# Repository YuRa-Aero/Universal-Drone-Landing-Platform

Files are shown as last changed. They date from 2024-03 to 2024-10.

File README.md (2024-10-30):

# Универсальная посадочная платформа для дронов

[][cc-by-nc]

[cc-by-nc]: https://creativecommons.org/licenses/by-nc/4.0/
[cc-by-nc-shield]: https://img.shields.io/badge/License-CC%20BY--NC%204.0-lightgrey.svg

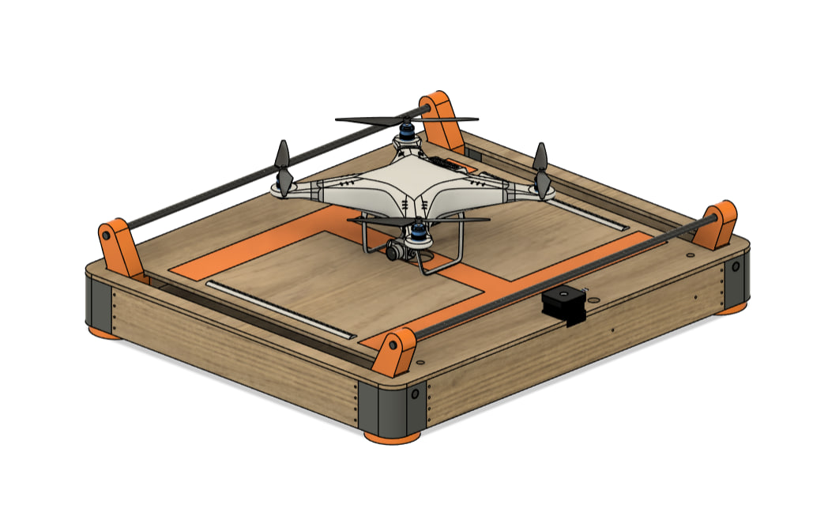
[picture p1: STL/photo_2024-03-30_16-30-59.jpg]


В данном проекте реализуется полная разработка готового изделия по техническому заданию с нуля в сжатый срок - 5 дней.

ТЗ *(подробнее см "ТЗ.pdf)* : разработать посадочную платформу для дронов различных размеров с фиксацией квадрокоптера после посадки

В ходе выполнения работы:
* Сделано эскизное проектирование
* Создан чертеж платформы *(Для изучения моделей см. "Чертеж.pdf)*
* Смоделирована подробная 3д модель, каждый узел подготовлен к 3д печати *(Для изучения моделей см. папку "STL")*
* Выполнена робототехническая часть
* Разработана инструкция по сборке
* Расчитана себестоимость с учётом производства
* Оформлена документация в формате PDF
## *Для более детального ознакомления с проектом см. "Документация.pdf" - 33стр.*
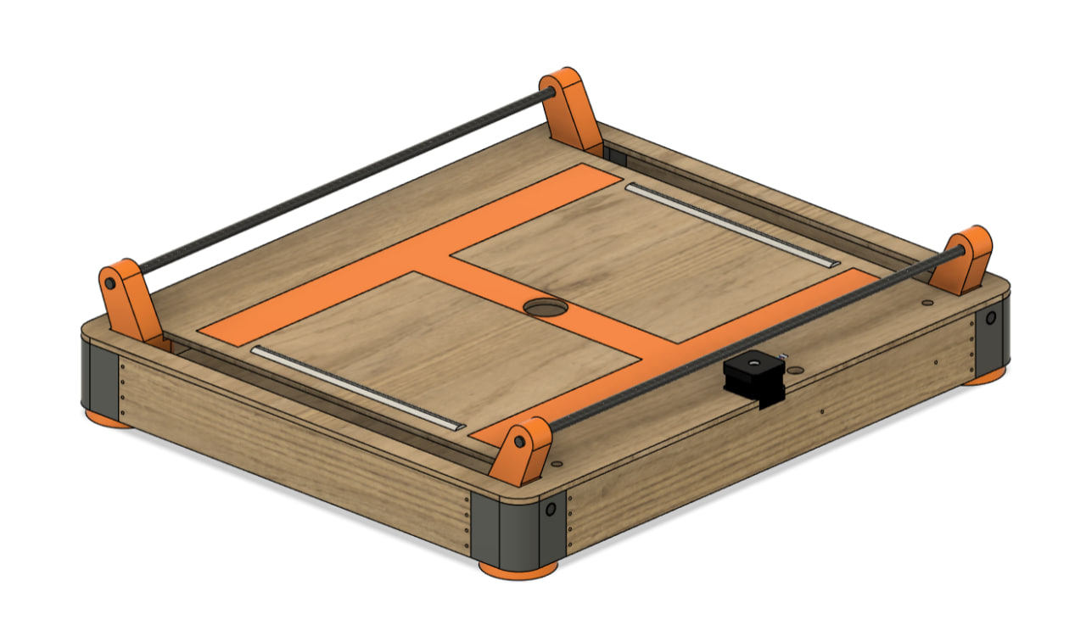
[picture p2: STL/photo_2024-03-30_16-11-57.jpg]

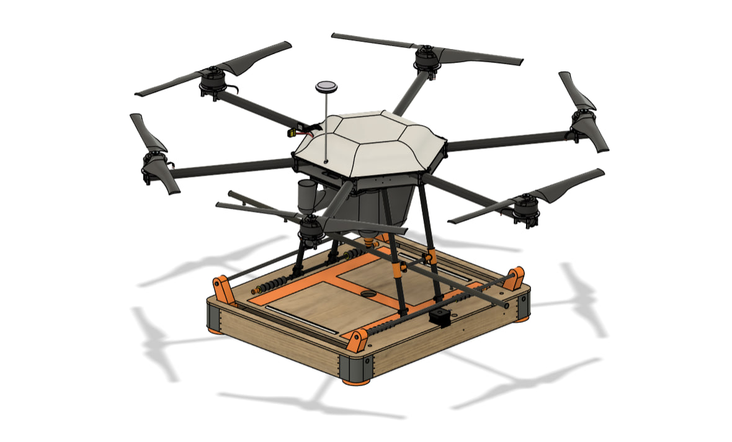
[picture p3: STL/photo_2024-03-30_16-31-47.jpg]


[][cc-by-nc]

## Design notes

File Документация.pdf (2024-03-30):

ЛНИП г. Королев

Проектная работа

### УНИВЕРСАЛЬНАЯ ПОСАДОЧНАЯ ПЛАТФОРМА ДЛЯ КВАДРОКОПТЕРОВ

Работа выполнена в рамках конкурсного задания на отбор в Артек 2024 «Реализация поставленного кейса на тему БЛА»

Выполнил:
Ученик 10 Б класса Куликов Юрий Наставник:
Куликов А.П.
2024

### Оглавление

Определение и разработка механической системы фиксации квадрокоптера на платформе после посадки. Определение необходимых дополнительных модулей и сенсоров с описанием их

### 8. По итогам анализа разработанного прототипа Платформы были выявлены следующие

0. Введение
0.1 Проблема
Посадка БЛА один из самых важных этапов полёта. На этом этапе происходит большинство случаев поломок БЛА, в том числе по следующим причинам:
- неровной поверхности на зоне посадке (склоны, рытвины, высокая трава и другие антропогенные факторы).
- неверное позиционирование зоны посадки оператором, в том числе через на FPV дронах
- неверное позиционирование посадочной зоны из-за плохих погодных условий – дождь, туман, тёмное время суток.
Также одной из востребованных задач после приземления дрона, является задача уменьшения времени «сворачивания» и смены позиции запуска дрона. Эта задача стоит перед обслуживающей дрон командой (расчётом).
0.2 Актуальность
В современных условиях активного использования дронов для решения различных задач, возникает потребность создания приспособления-устройства решить описанную проблему. Автономные взлетно-посадочные платформы для беспилотных летательных аппаратов используются для решения задач различного рода, в том числе для автоматической доставки продуктов, для военных задач, задач мониторинга и орошения в агропромышленном комплексе.
0.3 Цель
Необходимо разработать универсальную посадочную платформу для квадрокоптеров (далее- Платформа), предназначенную для различных применений.
0.4 Задачи
Задание 1. Эскизное проектирование:
Нарисовать эскиз будущей платформы (может быть нарисован с помощью чертёжных принадлежностей на листе бумаги, или графического планшета, или CAD-системы).

Задание 2. 3D-моделирование:
Создать 3D-модель(и) посадочной платформы с учетом габаритов и весовых характеристик квадрокоптеров различных типов и моделей.
Задание 3. Робототехническая часть:
3.1. Разработать механическую систему фиксации квадрокоптера на платформе после посадки.
3.2. Предусмотреть места для крепления и подключения дополнительных модулей и сенсоров, описать их назначение.
Задание 4. Программирование:
Разработать код для управления подсветкой посадочной платформы в зависимости от расстояния до приземляющегося квадрокоптера.
Задание 5. Производство:
Определить необходимые материалы для изготовления посадочной платформы с учетом прочности и легкости.
Задание 6. Бюджет:
Определить бюджет проекта.

0.5 Основная концепция
Основные допущения при создании универсальной посадочной платформы для квадрокоптеров:
✓ В части универсальности выбирается определённое семейство дронов размерами от DJI Phantom до агрокоптеров с вместимостью бака до 16л. Для квадрокоптеров большего типоразмера нужна доработка данного решения, с условиями масштабируемости. Для квадрокоптеров меньшего размера актуальность наличия Платформы является низкой. Но и для них может быть разработана уменьшенная версия Платформы.
✓ При выборе материалов для изготовления отдаётся предпочтение в сторону деталей изготовляемых способом 3D печати. Количество деталей из других материалов минимизируется.
✓ Материалы из стали не используются из-за сложности их обработки.
✓ В части электронной базы и датчиков решается задача баланса между стоимостью и функциональностью. Компонент выбирается за минимальную стоимость с необходимой функциональностью.
✓ Также решается задача максимально быстрого создания рабочего прототипа изделия, без выхода на промышленное производство, для отработки работоспособности прототипа
✓ Автономность. Предполагается автономное питание и обслуживание-переноска одним человеком.
✓ Предполагается использование в закрытых помещениях и на открытом воздухе. ✓ Предполагается что Платформа будет эксплуатироваться в температурных режимах от -5 до +40 градусов. При более низких температурах нужно вводить элементы подогрева, смазку и менее хрупкие материалы. При более высоких температурах возможен перегрев электронного блока и нарушение геометрии деталей распечатанных методом 3d печати.

0.6 Требования к оформлению результатов проекта в виде файлов и документов:
1. Документация в формате PDF:
✓ В этом файле должны быть описаны этапы выполнения задания.
✓ Разработанные эскизы, скриншоты хода выполнения работы, а также фотографии, должны быть приложены в этот файл.
✓ В этом файле должен быть представлен весь программный код, который был использован для выполнения задания.
2. 3D-модели в формате STL:
✓ Каждая модель должна быть представлена в отдельном файле с соответствующим названием.
✓ Файлы должны быть сохранены в формате STL, который является стандартом для обмена 3D-моделями.
1. Задание 1: Эскизное проектирование.
Создание эскиза-чертежа будущей платформы с помощью CAD-системы.

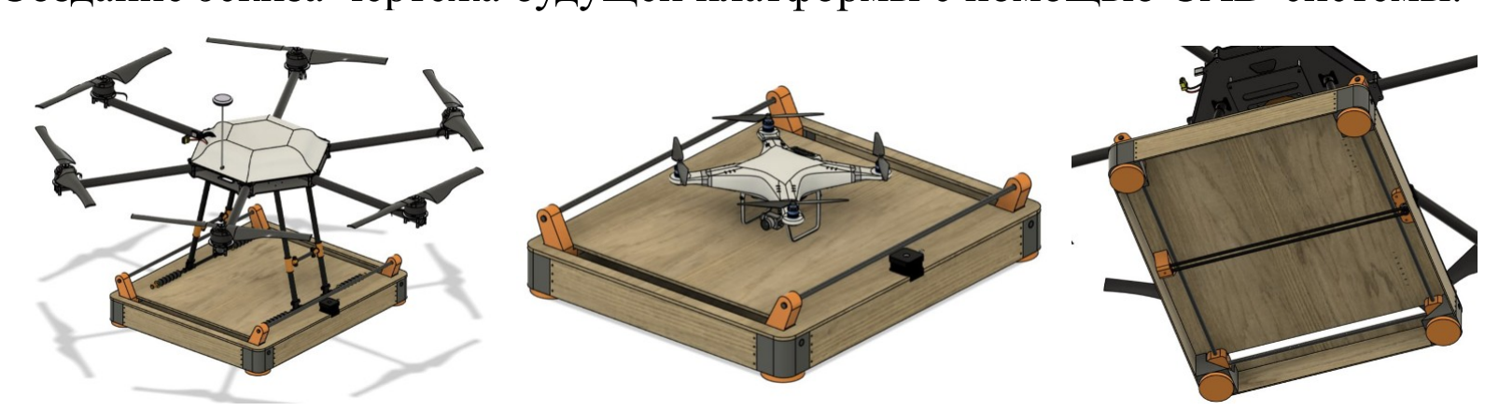
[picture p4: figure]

Рис. 1.1. Эскиз Платформы выполенный в Fusion360.

Описание принципов работы Платформы: Платформа устанавливается на поверхность, ножки позволяют производить небольшую регулировку для выравнивания. Включается питание платформы и переходит в режим ожидания прибытия БЛА. В это время для лёгкости обнаружения БЛА Платформа подсвечивается. Платформа оборудована дальномером и в момент обнаружения БЛА, готового для приземления, включается цветная подсветка. После приземления БЛА на платформу включаются механические захваты-толкатели, которые позиционируют и фиксируют БЛА. После нажатия кнопки оператором, захват освобождает БЛА для взлёта или снятия с Платформы. После этого Платформа заново переходит в режим готовности принятия нового БЛА.

Приведенные выше пластиковые детали (имеющие серый и оранжевый цвет на рендерах) были подготовлены к изготовлению на 3D принтере. Для этого модели деталей, разработанные в среде Fusion 360, были экспортированы в формат, использующийся в технологии быстрого прототипирования 3-D печати для хранения трехмерных моделей объектов stl. Полученный файл обрабатывается программой Prusa Slicer, которая и управляет режимом печати модели на принтере Prusa MK3S+.
Далее сборка Платформы в формате step была импортирована в программу Компас-3Д для создания чертежа модели по ГОСТу.

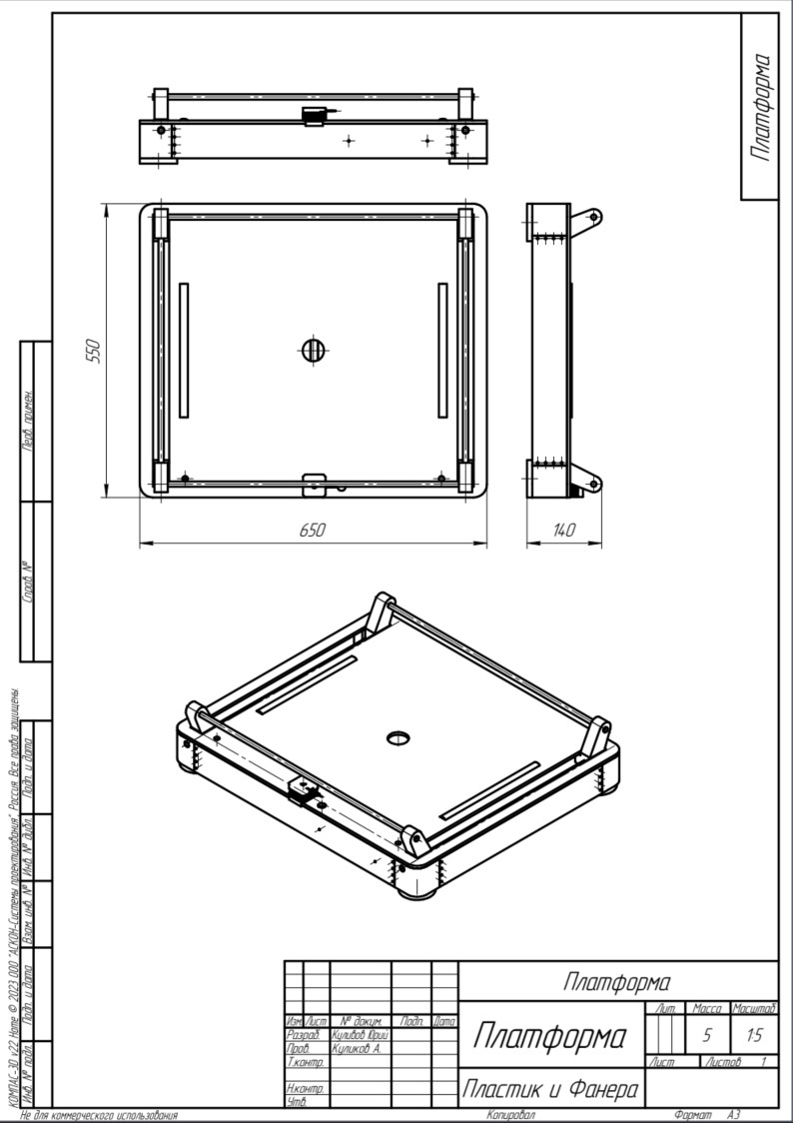
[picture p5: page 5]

Рис. 1.2 Чертёж в по ГОСТ выполенный в CAD системе КОМПАС-3D

Заключение: в ходе выполнения Задания 1 создан полноценный чертеж-эскиз Платформы:
- демонстрирующий идею проекта
- демонстрирующий принцип работы проекта,
- демонстрирующий его элементы
- эскиз образмерен и выполнен в цифровом виде в CAD-системе
- чертёж оформлен по ГОСТу
2. Задание 2: 3D-моделирование.
Создание 3D-модель(и) посадочной платформы с учетом габаритов и весовых характеристик квадрокоптеров различных типов и моделей
Проведён анализ текущих видов распространённых квадрокоптеров и видов их формы для разработки универсального захвата (Рис. 2.1 – Рис.2.4). Также дополниетльно, вне границы конкурсного задания рассмотрены мультикоптеры (Рис. 2.5)

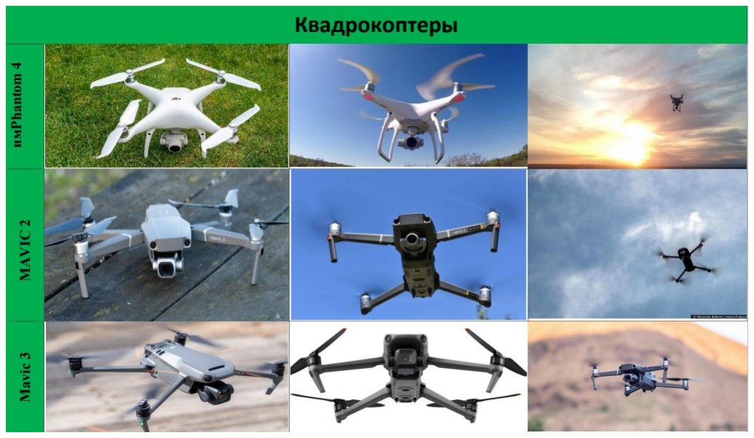
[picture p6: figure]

Рис. 2.1 Квадрокоптеры типа Mavic 2 Mavic 3 Phantom 4.

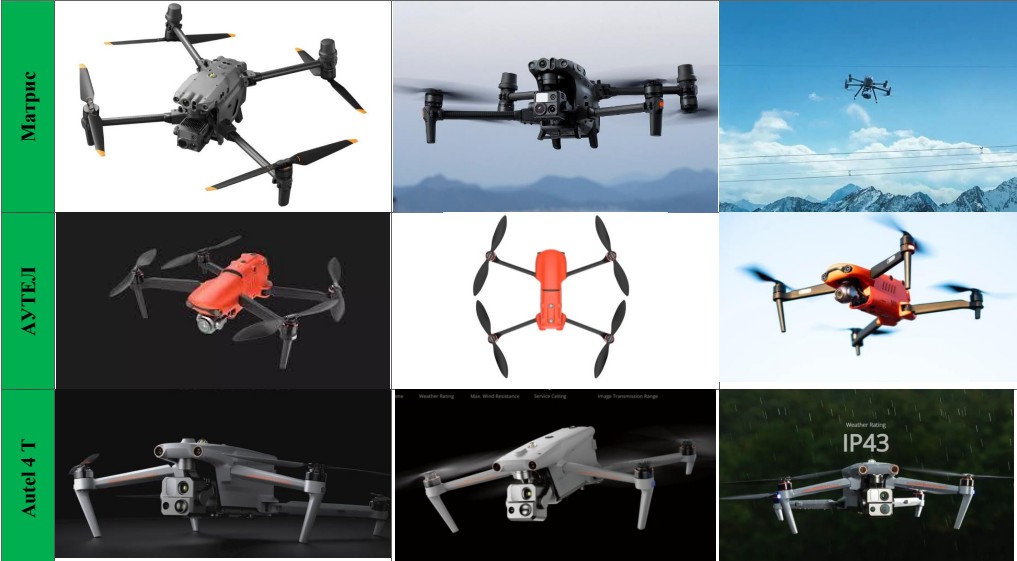
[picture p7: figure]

Рис. 2.2 Матрис, АУТЕЛ, Autel 4T.

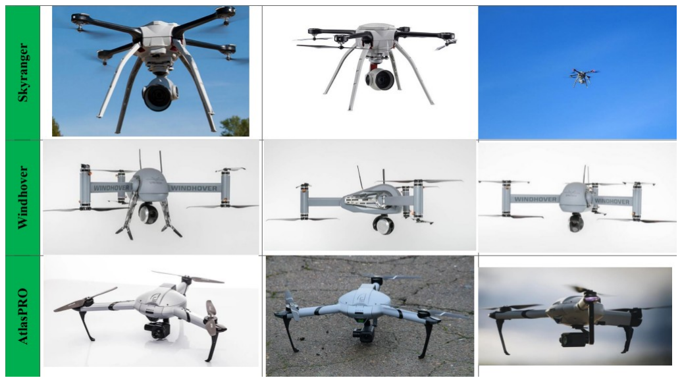
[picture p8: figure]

Рис. 2.3 Квадрокоптеры типа Skyranger, WindHover, AtlasPro.

Рис. 2.4 Квадрокоптеры типа Kargu m ½ Skydio X2.

Рис. 2.5 Мультикоптеры Matrice 600. Были проанализированы текущие решения посадочных платформ и типов захвата. Наиболее полно информация раскрыта статьёй на Хабре. [12]. Наиболее перспективным видом толкателей посчитал W и V образные толкатели. См. Рис. 2.6 Где слева: посадочная платформа с W-образными толкателями для позиционирования: 6 - БПЛА; 401 - толкатели W-образными кромками. Справа: Посадочная платформа с V-образными толкателями для позиционирования: 810 - ножка БПЛА; 220 - толкатели с V-образными кромками.

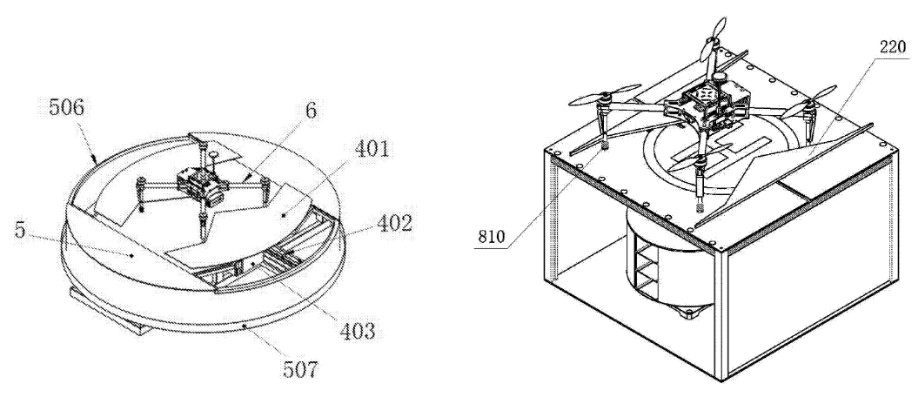
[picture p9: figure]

Рис. 2.6 W и V образные толкатели

Но учитывая, что большинство агродронов (см. Рис 2.7) используют опорную конструкцию в виде пользьев, такой вид толкателей не стал выбирать. Так как для полозьев данный вид захвата не эффективен

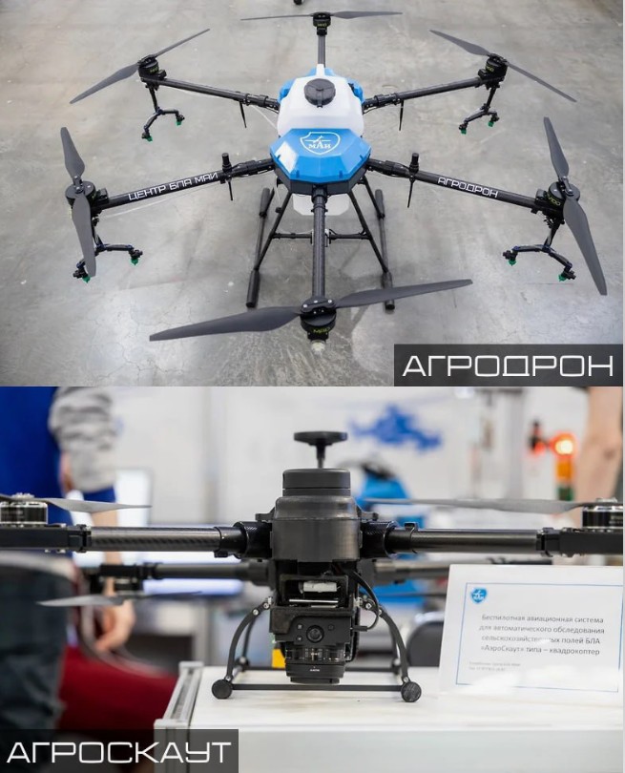
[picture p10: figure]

Рис. 2.7. «Агроскаут» и «Агродрон» от МАИ.

В итоге был выбран захват в виде двух толкателей прямой формы. Параллельные толкатели. Базовый принцип и примеры были изложены в статье на Хабре. [12]. Рис. 2.8. Толкатели в виде планок передвигают БЛА в требуемую зону позиционирования. Наиболее часто используются одна или две пары параллельных друг другу и работающих синхронно толкателей, сдвигающих БЛА за опоры (ножки) к центру посадочной площадки. Данный вид показался мне переспективным с учётом того, что в дальнейшем платформу можно оснастить зарядной станцией. Тогда будет удобно сдвигать БЛА к центру Платформы, где обычно расположены контакты питания. Как дополнительная возможность - толкатели могут содержать элементы крепления с электрическими контактами.

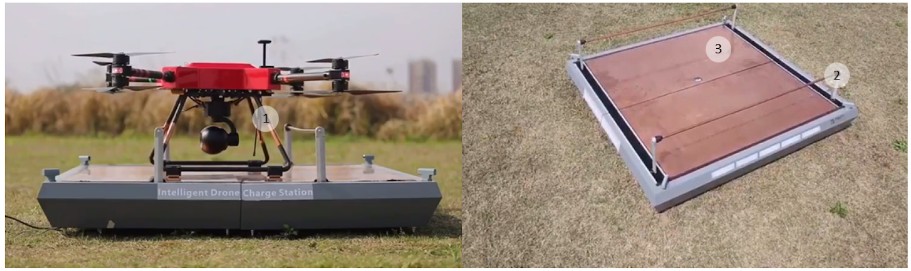
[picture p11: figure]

Рис. 2.8. Платформа Ewatt Aerospace. 1 - опора БЛА с электродами; 2 - посадочная площадка; 3 - толкатели с электродами

Процесс 3 D моделирования:
Примичание: все операции выполнялись с помощью твердотельного моделирования. Детали серого и оранжевого цвета — пластиковые. Детали с текстурой древисины — из фанеры
-С учётом типоразмеров дронов была смоделирована площадка 650х550мм:

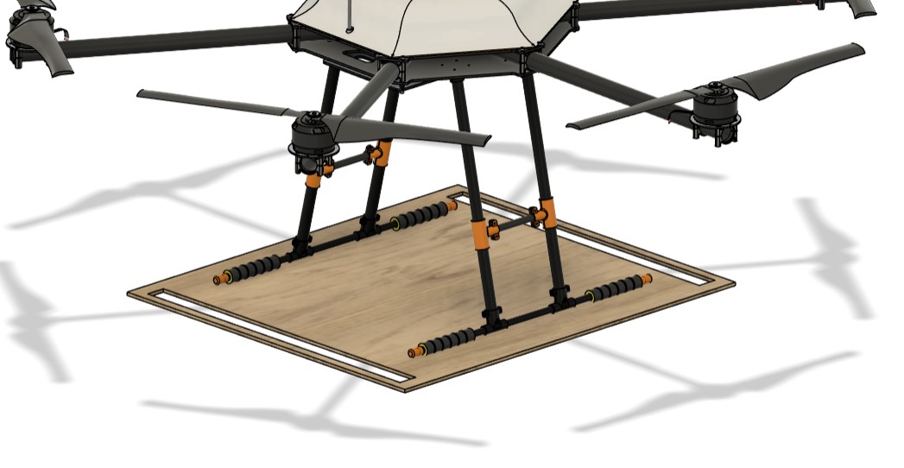
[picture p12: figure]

Рис. 2.9. Площадка
В качестве материала для площадки используется фанера 6мм. К модели применен соответствующий материал (текстура)

Она была выбрана по соотношению

цены/прочности/обрабатываемости

- прочностные характеристики фанеры разной толщины

-Следующим шагом были смоделированаы каретки хватателей:

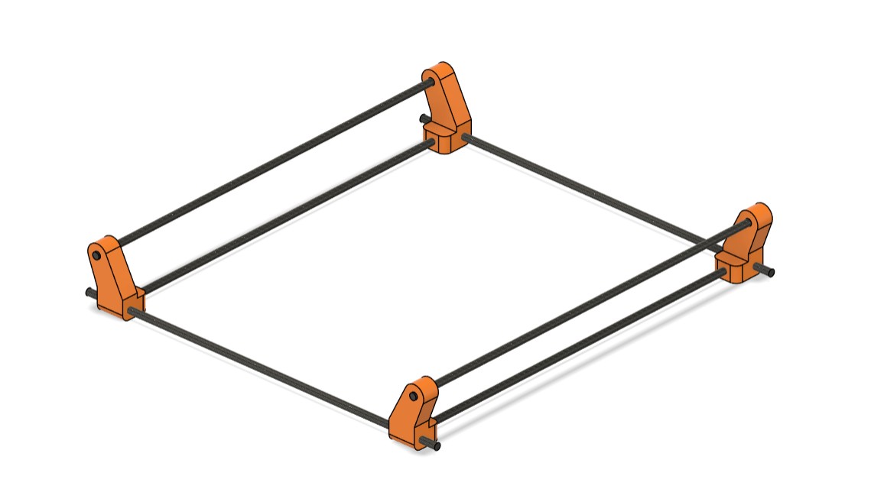
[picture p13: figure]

Рис. 2.10. Кинематика хватателей В качестве направляющих были использованы трубки диаметром 10мм

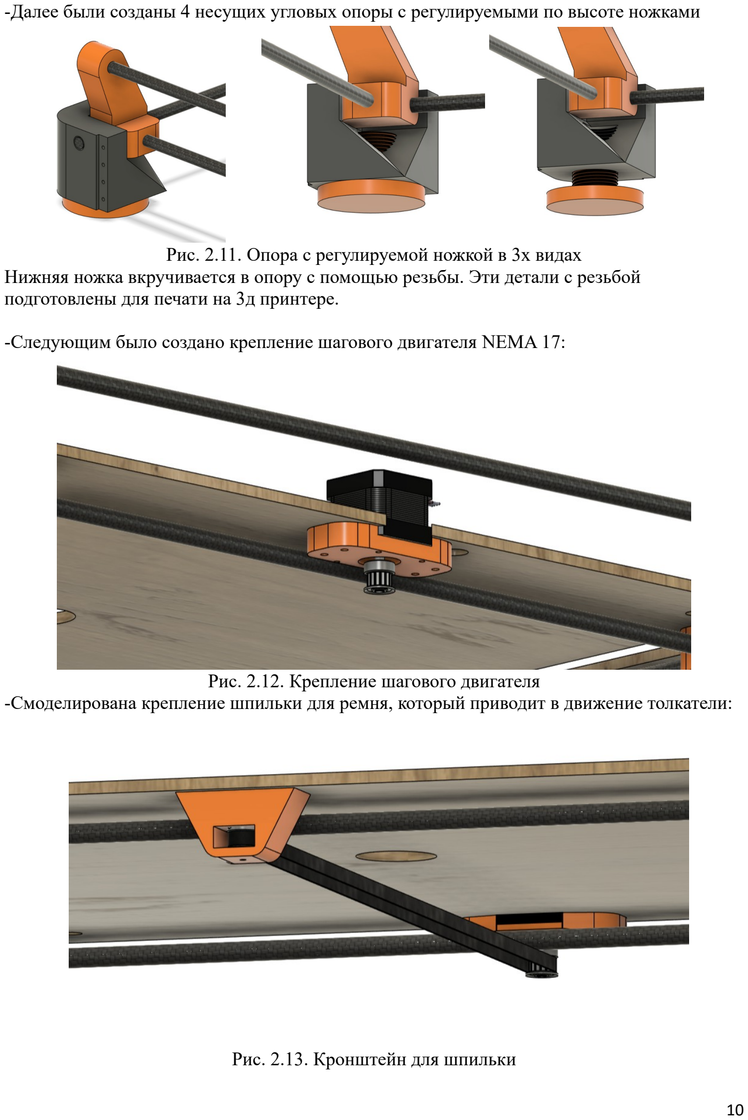
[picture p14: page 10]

-Далее были созданы 4 несущих угловых опоры с регулируемыми по высоте ножками

Рис. 2.11. Опора с регулируемой ножкой в 3х видах Нижняя ножка вкручивается в опору с помощью резьбы. Эти детали с резьбой подготовлены для печати на 3д принтере.

-Следующим было создано крепление шагового двигателя NEMA 17:

Рис. 2.12. Крепление шагового двигателя -Смоделирована крепление шпильки для ремня, который приводит в движение толкатели:

Рис. 2.13. Кронштейн для шпильки

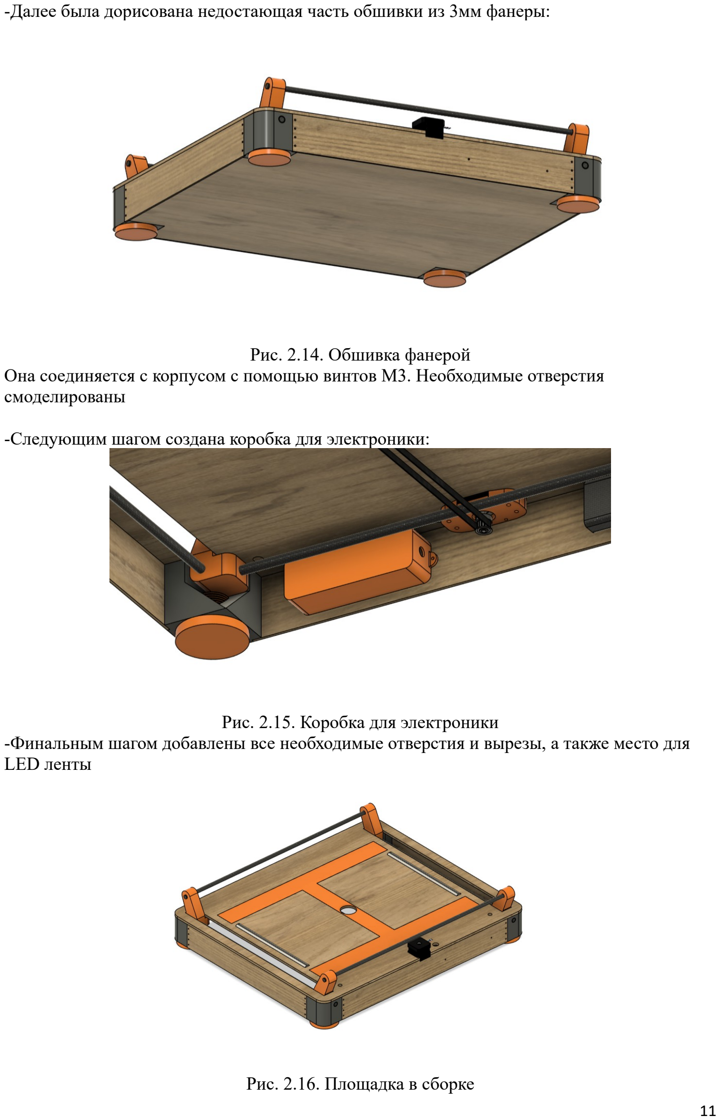
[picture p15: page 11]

-Далее была дорисована недостающая часть обшивки из 3мм фанеры:

Рис. 2.14. Обшивка фанерой Она соединяется с корпусом с помощью винтов М3. Необходимые отверстия смоделированы

-Следующим шагом создана коробка для электроники:

Рис. 2.15. Коробка для электроники -Финальным шагом добавлены все необходимые отверстия и вырезы, а также место для LED ленты

Рис. 2.16. Площадка в сборке

Таким образом была создана сборка всех деталей проекта.
Все детали для 3D печати (серый/оранжевый) экспортированы в формат .stl
Все детали для ЧПУ фрезеровки (фанера) экспортированы в формат .dxf

Заключение: в ходе выполнения Задания 2 созданы 3D-модель(и) Платформы:
- с учетом габаритов и весовых характеристик квадрокоптеров различных типов и моделей;
- 3D-модели разработаны с помощью полигонального или твердотельного моделирования;
- наличествует сборка разработанных деталей проекта в единую конструкцию;
- Применены материалы/текстуры, которые используют технические возможностей программ в добавлении текстур или материалов к 3D-моделям/сборке.
3. Задание 3: Робототехническая часть.
Определение и разработка механической системы фиксации квадрокоптера на платформе после посадки. Определение необходимых дополнительных модулей и сенсоров с описанием их назначения. Описание мест для их крепления и подключения.

Выбор микроконтроллера и аргументация выбора:
При выборе основного управляющего элемента были рассмотрены текущие предложения на рынке с учетом стоимости и их распространения. В результате выборки были выбраны две платформы Rusberry и Arduino. После сравнения выбор был остановлен на Arduino: Arduino - это удобная платформа быстрой разработки электронных устройств и электронный конструктор для новичков и профессионалов. Платформа пользуется огромной популярностью во всем мире благодаря удобству и простоте языка программирования, а также открытой архитектуре и программному коду.
Arduino – комбинация аппаратной и программной частей для простой разработки электроники.
Аппаратная часть включает в себя большое количество видов плат Arduino со встроенными программируемыми микроконтроллерами, а также дополнительные модули. Программная часть состоит из среды разработки (программы для написания скетчей и прошивки микроконтроллеров Arduino), упрощенного языка программирования, огромного множества готовых функций и библиотек.
Существует несколько версий платформ Arduino: Leonardo, Uno, Nano, Due.
Версия UNO является одной из самых популярных и широко используемой для небольших проектов.
Программирование | микроконтроллеров | Arduino | осуществляется | на | языке
программирования С/C++.
Контроллер Arduino Uno построен на платформе ATmega328, имеющей 14 цифровых входов/выходов (6 из которых могут использоваться как выходы ШИМ), 6 аналоговых входов, кварцевый генератор 16 МГц, разъем USB, силовой разъем, разъем ICSP и кнопку перезагрузки (см. таблицу №1). Для работы необходимо подключить платформу к компьютеру посредством кабеля USB, либо подать питание при помощи адаптера или батареи.

Таблица 3.1 характеристики контроллера

Технические характеристики Arduino Uno Rev 3
Микроконтроллер | ATmega328P

Рабочее напряжение | 5 V
Входное напряжение (Рекомендуемое) | 7-12 V
Входное напряжение (Ограничение) | 6-20 V
Цифровые (I/O) Пины | 14 (4 for PWM Output)
PWM Цифровые (I/O) Пины | 6
Аналоговый вход Пины | 6
Постоянный ток на I/O Пин | 20 mA
Постоянный ток для 3.3 V Пин | 50 mA
Флэш-память | 32 KB (.5 KB для загрузчика)
SRAM | 2 KB
EEPROM | 1 KB
Тактовая частота | 16 MHz
LED встроенные | 13
Длина | 68.6 mm
Ширина | 53.4 mm
Вес | 25 g

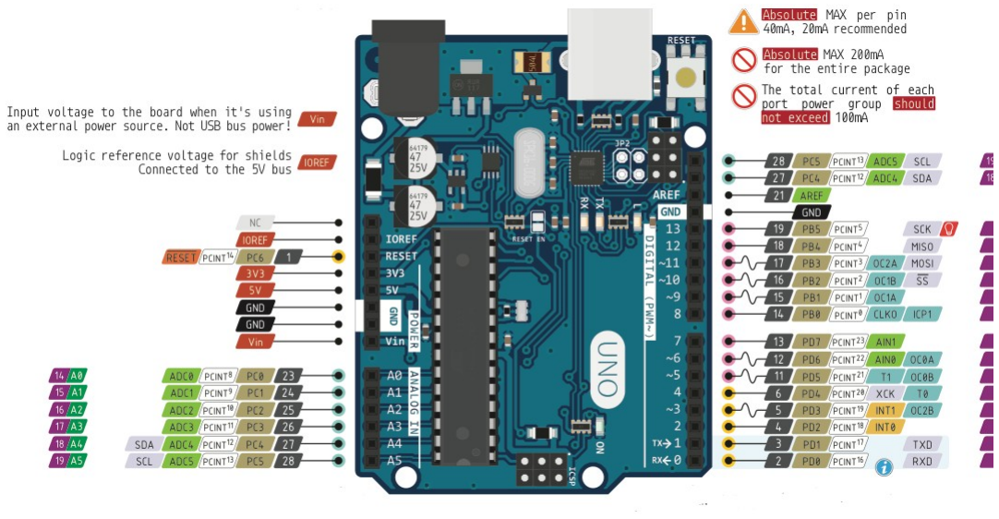
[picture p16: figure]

Рис 3.1. Назначение выводов контроллера Arduino Uno

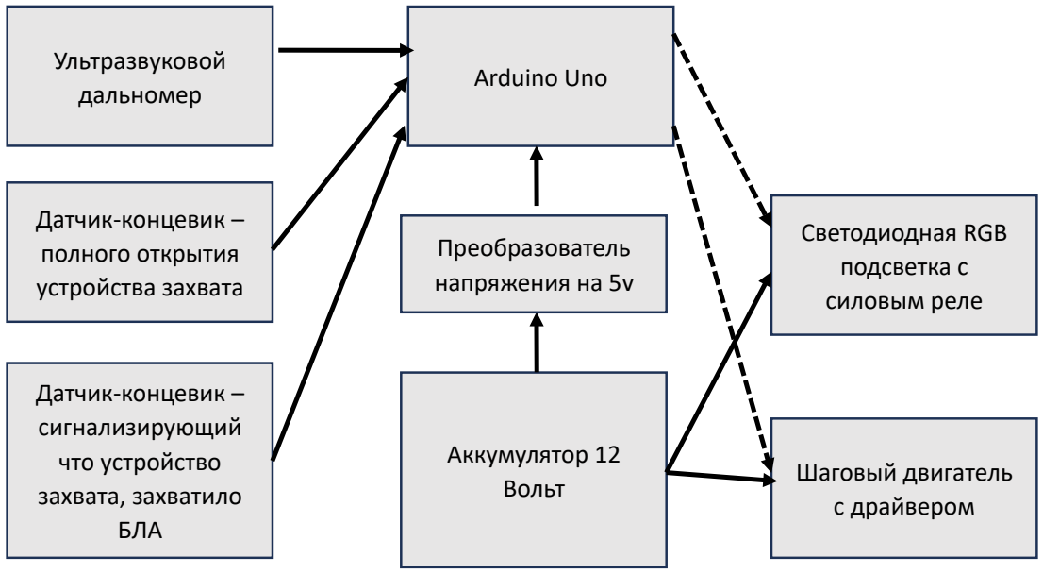
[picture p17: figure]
Arduino Uno Ультразвуковой дальномер; Датчик-концевик – полного открытия устройства захвата; Датчик-концевик – сигнализирующий что устройство захвата, захватило БЛА; Светодиодная RGB подсветка с силовым реле; Шаговый двигатель с драйвером; Аккумулятор 12 Вольт; Преобразователь напряжения на 5v

Рис.3.2. Структурная схема электр. элементов Платформы

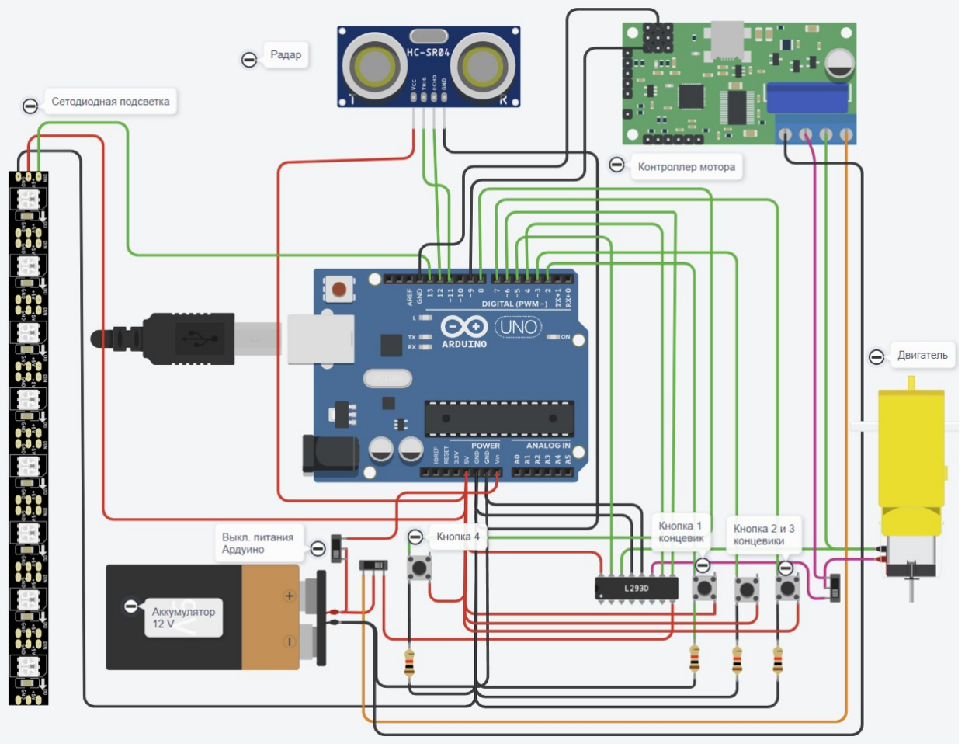
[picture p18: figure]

Рис. 3.3 Электронный макет проекта в ПО Thinkercad.

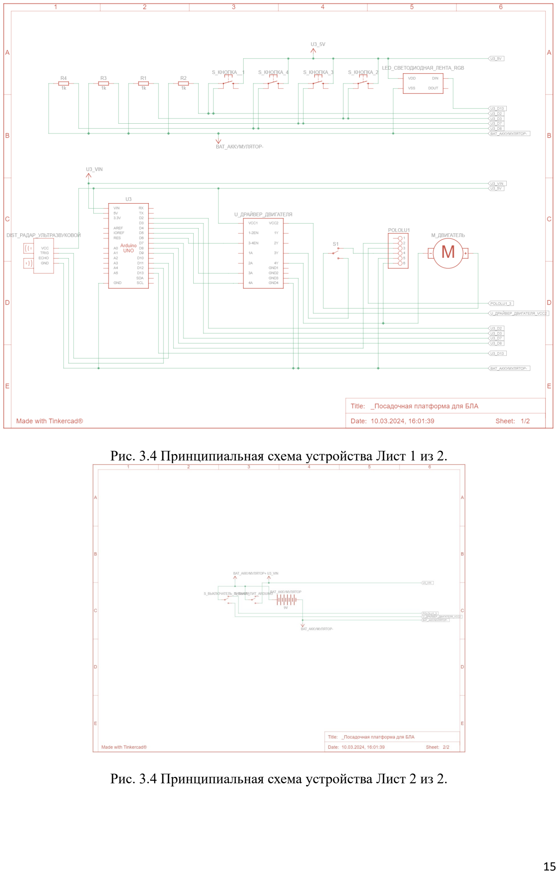
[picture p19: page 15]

Рис. 3.4 Принципиальная схема устройства Лист 1 из 2.

Рис. 3.4 Принципиальная схема устройства Лист 2 из 2.

Выбор датчиков:

Ультразвуковой дальномер HC-SR04
Для решения задачи определения приближающего БЛА и активизации световой индикации Платформы необходимо выбрать подходящий тип датчика.
Проводили выбор датчика для измерения расстояния до квадрокоптера среди инфракрасных, лазерных, видекамеры.
Была выбран инфракрасный датчик из-за следующих его преимуществ:
- доступная стоимость;
- низкую заметность к обнаружению;
- относительно высокую защищенность от помех, перепадов температуры, влажности воздуха, освещенности.

Среди вариантов для Ардуино был выбран ультразвуковой дальномер HC-SR04 Ультразвуковой датчик способен определять расстояние до объектов от двух до 450 см. Практические исследования показали, что наибольшая точность достигается при угле меньше 30 градусов. Разрешение 0,3см. Принцип действия заключается в следующем: датчик отправляет ультразвуковые сигналы, которые отражаясь от объекта,
возвращаются обратно. По задержке отраженного сигнала определяется расстояние до объекта. Точность и практичность этого ультразвукового датчика позволяют
использовать его в качестве дальномера.

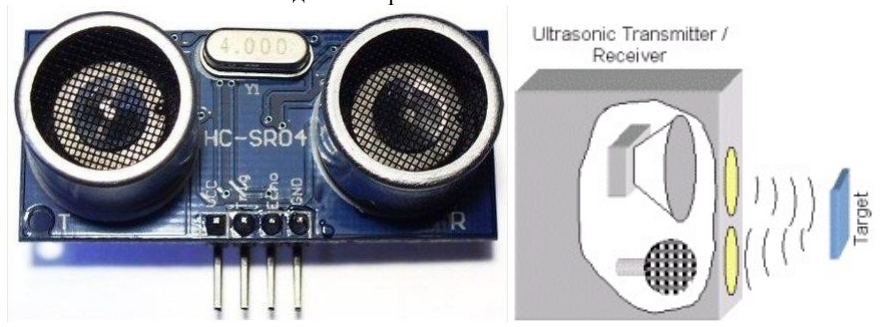
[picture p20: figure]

Рис. 3.6 Ультразвуковой дальномер

Разработка электрической схемы с датчиками была смоделирована в виртуальной среде отладки макетных плат Tinkercad [13] (см. рисунок 3.3).

Выбор системы позиционирования и захвата БЛА после посадки на платформу Сравнивались три вида позиционирования:
– без устройств позиционирования;
– с активными устройствами позиционирования;
– с пассивными устройствами позиционирования;
– с комбинацией устройств позиционирования.

В ходе исследования была выбрана вид посадочной платформы с активными устройствами позиционирования в виде параллельных толкателей. В конструкцию толкателя входят шаговый двигатель и линейные направляющие. Толкатели в виде двух планок передвигают БЛА в требуемую зону позиционирования.

Для программирования системы позиционирования дрона на основе микроконтроллера Arduino Mega использовалась библиотека Stepper, позволившая управлять шаговым двигателем. Библиотека Stepper предоставляет удобный интерфейс управления биполярными и униполярными шаговыми двигателями. В программе применялась команда StepsPerRevolution. Для работы с шаговыми двигателями в библиотеке Stepper была задействована команда вида stepper.set Speed (200). Затем, чтобы двигатель сделал один шаг, можно использовать команду stepper.step(val). Количество шагов, которое должен сделать двигатель, определяется переменной «val».Чтобы шаговый двигатель сделал один шаг по часовой стрелке, необходимо использовать команду stepper.step(1).

Шаговый двигатель Nema 17, 34 мм, 26 см (36,8 унций), а, 12 В, Nema17, шаговый
двигатель 42BYGH, 4-проводной ЧПУ Reprap 3D-принтер | AliExpress (https://aliexpress.ru/item/32907886993.html?sku_id=65956580901&spm=.search_results.0.58b042d46Z9e8T)

Рис. 3.7 Шаговый двигатель Nema

Драйвер управления шаговым двигателем HW-130 motor control shield for Arduino

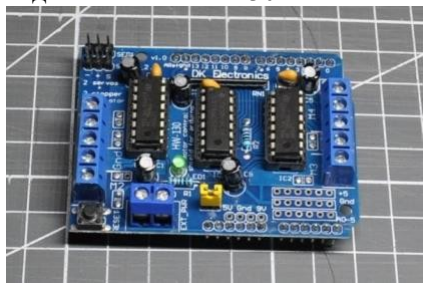
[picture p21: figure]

Рис. 3.8 Драйвер управления шаговым двигателем

Кнопка тактовая 12х12 KLS7-TS1204

Рис. 3.9 Кнопка - концевик

Преобразователя напряжения (12->5 В)
На Платформе смонтирован аккумулятор 12 вольт. Он же питает плату Ардуино, где предусмотрен вход Vin с диапазоном от +6V до +12V. См. Рис. 3.1 Поэтому дополнительного понижающего модуля питания не требуется.

LED RGB лента
В качестве источника подсветки была выбрана светодиодная лента.
Каждый светодиодный чип состоит из трех цветов и может изменять яркость в диапазоне от 0 до 255, модули могут объединяться для передачи сигналов по одной линии. Подсветка управляется с Ардуино через 1 управляющий контакт.

Модуль светодиодный адресный на чипах WS2812 5050 RGB 8 светодиодов Neopixel led С напряжением 5В и весом 3 г.

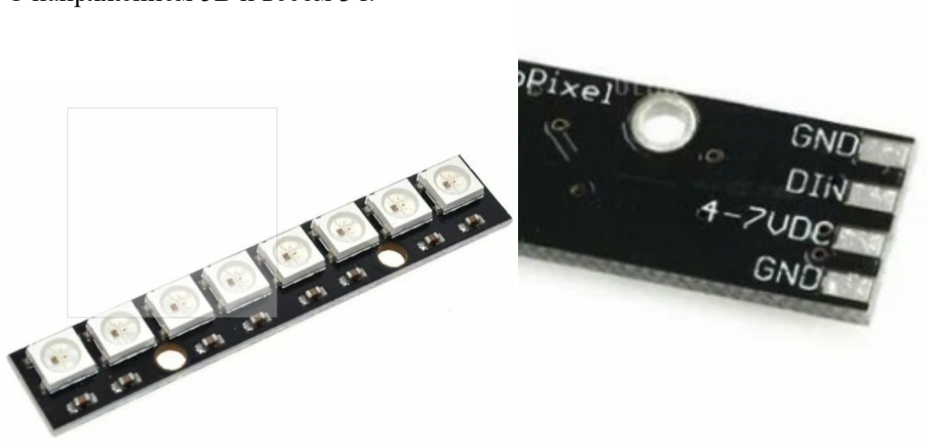
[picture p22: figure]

Рис. 3.10 LED RGB лента

Аккумулятор
Используются литиевые аккумуляторы, емкостью 2200 МА\Ч, с
напряжением 12 В. Оценочно этого хватает на ХХХ часа в рабочем режиме. При таких характеристиках аккумулятор обладает малой массой и габаритами. Смена осуществляется оперативно, что помогает быстро менять батареи и не прерывать работу Платформы на длительное время.

Вспомогательных детали: резисторы, макетная плата.
Все эти детали нужны для согласования элементов Платформы и световой индикации работы Платформы

Монтажная плата (1 штука)

Рис. 3.11 Монтажная плата

Соединительные провода

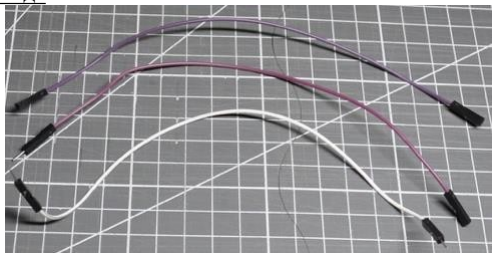
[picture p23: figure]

Рис. 3.12 Соединительные провода

Заключение: в ходе выполнения Задания 3 создана робототехническая часть Платформы:
- разработана электрическая схема с применением микроконтроллерной платы Arduino;
- использованы элементы схемотехники;
- применены цифровые датчики;
- разработка выполнена в виртуальной среде.
4. Задание 4: Программирование.
Разработка кода для управления Платформы, включая управление подсветкой посадочной платформы в зависимости от расстояния до приземляющегося квадрокоптера.
Блок - схема алгоритма программы

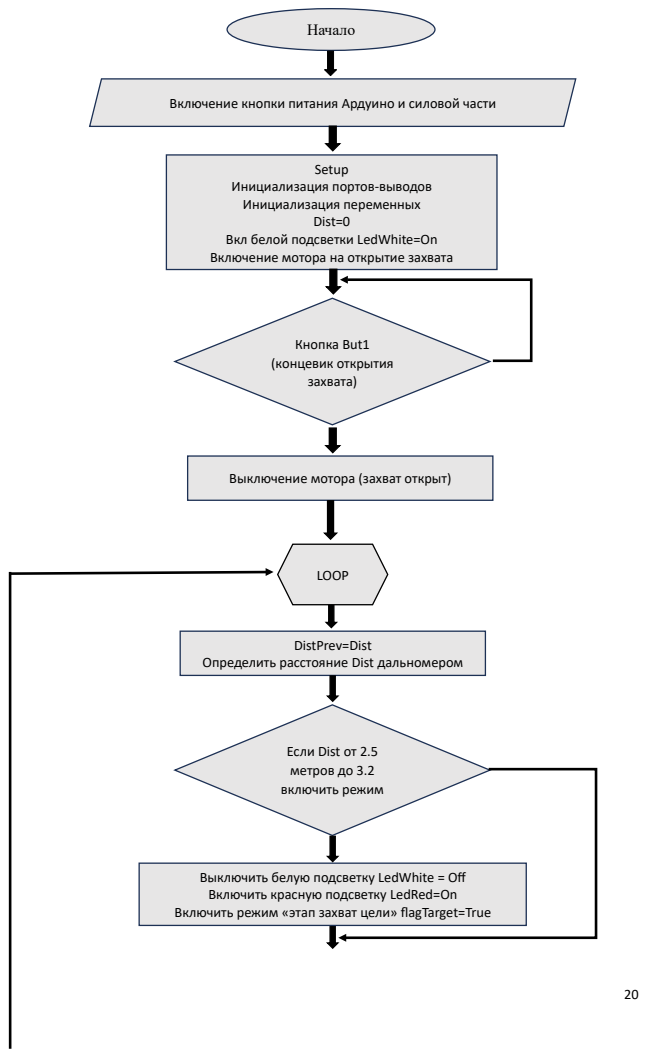
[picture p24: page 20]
Начало; Кнопка But1 (концевик открытия захвата); Setup; Dist=0; LOOP; DistPrev=Dist

Включение кнопки питания Ардуино и силовой части

Инициализация портов-выводов
Инициализация переменных

Вкл белой подсветки LedWhite=On
Включение мотора на открытие захвата

Выключение мотора (захват открыт)

Определить расстояние Dist дальномером

Если Dist от 2.5
метров до 3.2
включить режим

Выключить белую подсветку LedWhite = Off
Включить красную подсветку LedRed=On
Включить режим «этап захват цели» flagTarget=True

Отключить режим «этап захват цели» flagTarget=False

Отключить режим «этап захват цели» flagTarget=False

Если объект неподвижен более 5 секунд – считаем что

Объект захвачен – отключаем двигатели Motor=Stop

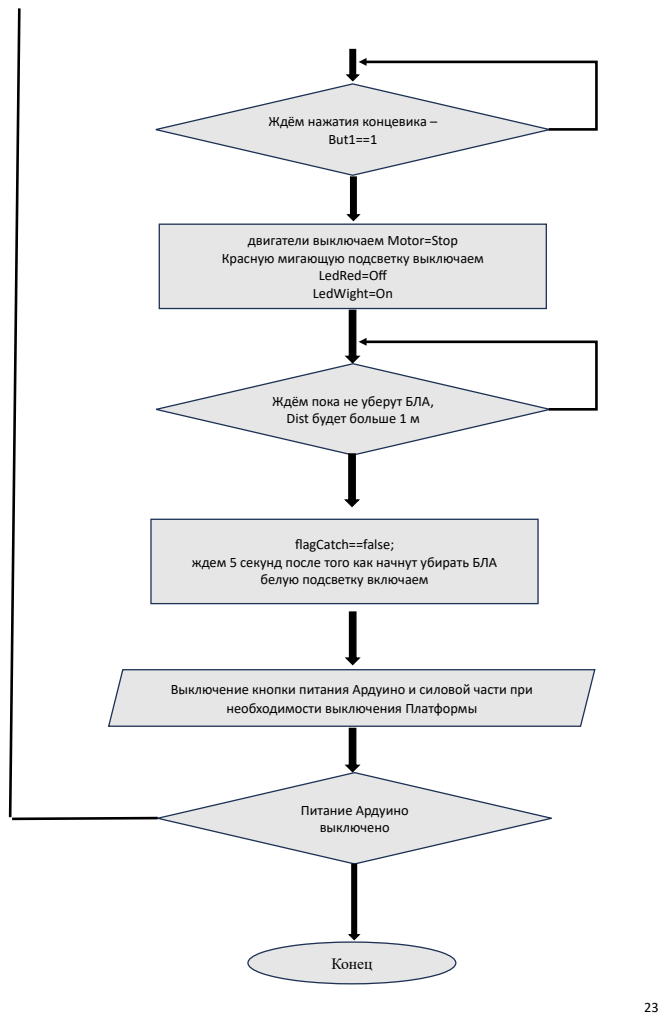
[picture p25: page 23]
But1==1; LedRed=Off LedWight=On; Конец; Питание Ардуино выключено; flagCatch==false;

Ждём нажатия концевика –

двигатели выключаем Motor=Stop
Красную мигающую подсветку выключаем

Ждём пока не уберут БЛА,
Dist будет больше 1 м

ждем 5 секунд после того как начнут убирать БЛА

белую подсветку включаем

Выключение кнопки питания Ардуино и силовой части при

необходимости выключения Платформы

Код программы автоматического управления Платформой: механизмами захвата и подсветкой.

// C++ code
#define __DEBUG 0

#include <Servo.h>

unsigned long TimerStart=millis(); // переменная времени в миллисекундах от начала работы Ардуино

boolean flagStandby = false; //Переменная режима ожидания
boolean flagTarget = false;
boolean flagPreLanding = false;
boolean flagLanding = false;
boolean flagCatch = false;

String strDebug ="";

int Dist = 0; //Переменная для считывания показаний с дальномера
int DistPrev = 0; //Переменная для показаний с дальномера в предыдущий момент времени

int But1 = 2; // 1-й датчик касания -концевик полного открытия устройства захвата
int But2 = 3; // 2-й датчик касания -концевик срабатывания устройства захвата на 1-й рамке
int But3 = 7; // 3-й датчик касания -концевик срабатывания устройства захвата на 2-й рамке
int But4 = 8; // 4-й датчик касания – кнопки управления – включить движение – освободить захваченный БЛА

// подключение драйвера двигателя для управления двигателем
int IN1Pin = 4; //микросхемы и управления
int IN2Pin = 5; //пины для подключения микросхемы
int Enable1Pin = 6; //обмоткой двигателя

int pinTrig = 11;
int pinEcho = 12;
// функция определения расстояния в сантиметрах дальномером long getDist() {
long duration, distance;
digitalWrite(pinTrig, LOW);
delayMicroseconds(2);
digitalWrite(pinTrig, HIGH); delayMicroseconds(10);
digitalWrite(pinTrig, LOW); duration=pulseIn(pinEcho, HIGH); return (duration/2) / 29.1;
}

//int cm = 0;

#include <Adafruit_NeoPixel.h>

int LedPin = 13; // Вывод управления включением/выключением светодиодами #define PIN 13 // input pin Neopixel is attached to

#define NUMPIXELS 8 // number of neopixels in strip

Adafruit_NeoPixel pixels = Adafruit_NeoPixel(NUMPIXELS, LedPin, NEO_GRB + NEO_KHZ800);

int delayval = 100; // timing delay in milliseconds

int redColor = 0;
int greenColor = 0;
int blueColor = 0;
// setColor()
// picks random values to set for RGB
void setColor(int redColor,int greenColor, int blueColor){
for (int i=0; i < NUMPIXELS; i++) {
// pixels.Color takes RGB values, from 0,0,0 up to 255,255,255 pixels.setPixelColor(i, pixels.Color(redColor, greenColor, blueColor)); // This sends the updated pixel color to the hardware. pixels.show();
// Delay for a period of time (in milliseconds).
//delay(delayval);
}
}

int buttonState = 0;
int ButTest = 8;
Servo motor;
#define PIN_PWM 9

//****************************************************************** //метод закрытия захвата
void MotorForward (){
digitalWrite(Enable1Pin,HIGH);//включаем обмотку двигателя //подаем напряжение так, чтобы двигатель вращался в одну сторону digitalWrite(IN1Pin,HIGH);
digitalWrite(IN2Pin,LOW);
TimerStart =millis(); // Запоминаем этот временной момент while(digitalRead(But2)!= HIGH && digitalRead(But3)!= HIGH ){ //while(digitalRead(But2)!= HIGH ){
delay(100);
if ( millis()-TimerStart > 10000){
break;
}
} // ждем пока захват полностью не захватит БЛА и не нажмет обе кнопки концевиков одновременно и ставим задержку чтобы избавиться от дребезга кнопки
digitalWrite(Enable1Pin,LOW); //отключаем двигатель
}
//метод открытия захвата
void MotorBackward (){
digitalWrite(Enable1Pin,HIGH);//включаем обмотку двигателя
//подаем напряжение так, чтобы двигатель вращался в обратную сторону digitalWrite(IN1Pin,LOW);
digitalWrite(IN2Pin,HIGH);

if (__DEBUG !=0) {
Serial.println(digitalRead(But1));
}
while(digitalRead(But1) != HIGH){
delay(100);
} // ждем пока захват полностью не откроется и не нажмет кнопку концевика digitalWrite(Enable1Pin,LOW); //отключаем двигатель
}

////////////////////////////
void setup()
{
pinMode(But1, INPUT ); //Объявление порта кнопки1 pinMode(But2, INPUT ); //Объявление порта кнопки2 pinMode(But3, INPUT ); //Объявление порта кнопки3
pinMode(But4, INPUT ); //Объявление порта кнопки4

pinMode(pinTrig, OUTPUT); //Объявление порта дальномера - источник
pinMode(pinEcho, INPUT); //Объявление порта дальномера – локатор-приёмник

Serial.begin(9600); // открываем последовательный порт - для вывода отладочной информации
motor.attach(PIN_PWM);
pixels.begin(); // Initialize the NeoPixel library.
setColor(255,255,244);//включаем белую подсветку

//устанавливаем все пины двигателя как выводы pinMode(Enable1Pin, OUTPUT);
pinMode(IN1Pin, OUTPUT);
pinMode(IN2Pin, OUTPUT);

digitalWrite(Enable1Pin,LOW); //отключаем обмотку MotorBackward (); // инициализация - открываем захват

// pinMode(ButTest, INPUT);
// pinMode(LED_BUILTIN, OUTPUT);
}
///////////////////////////
void loop()
{
uint32_t sec = millis() / 1000ul; // полное количество секунд int timeHours = (sec / 3600ul); // часы
int timeMins = (sec % 3600ul) / 60ul; // минуты
int timeSecs = (sec % 3600ul) % 60ul; // секунды //Serial.print("Time sec:"); //Serial.print(timeSecs);
//Serial.println("Loop start ");

DistPrev=Dist;
Dist = getDist();
// Если Dist от 2.5 метров до 3.2 включить режим захват цели
if (250 <= Dist && Dist <= 320){
setColor(255,0,0);// Включить красную подсветку LedRed=On flagTarget=true; //Включить режим «этап захват цели» flagTarget=True strDebug = strDebug + " Mode = flagTarget";
}
// Если Dist от 0,35 до 1 м включить режим предПосадка
if ( 35 <= Dist && Dist <= 100){
setColor(255,255,0);// Включить желтую подсветку
flagTarget=false; // Отключить режим «этап захват цели» flagTarget=False flagPreLanding=true; //Включить режим «этап предПосадка»
strDebug = strDebug + " Mode = flagPreLanding";
}
// Если Dist < 0,35 и flagPreLanding==True включить режим Посадка if (Dist < 35 && flagPreLanding==true){
//flagPreLanding =false; //
flagTarget=false;
flagLanding=true;
strDebug = strDebug + " Mode = flagLanding";
}
// Если Dist < 0,35 и flagLanding==True и Dist ==DistPrev
if (Dist < 35 && flagLanding==true && Dist ==DistPrev && flagPreLanding ==true){ TimerStart =millis(); // Запоминаем этот временной момент

flagPreLanding =false;
}
// Если Dist < 0,35 и flagLanding==True и Dist ==DistPrev и Time -TimerStart > 5 сек
if (Dist < 35 && flagLanding==true && Dist ==DistPrev && millis()-TimerStart > 5000){
// Если объект неподвижен более 5 секунд – считаем что дрон приземлился и включаем захват setColor(0,255,0);// Зелёную подсветку включаем LedGreen=On
MotorForward (); // Включаем мотор на захват Motor=Forward
setColor(0,0,0); //Зелёную подсветку выключаем LedGreen=Off
flagLanding=false;
flagPreLanding =false;
flagCatch = true;
strDebug = strDebug + " Mode = flagCatch";
}
// Ждём нажатия кнопки – чтобы освободить дрон ReleaseBut ==ON
if (flagCatch==true && digitalRead(But4)== HIGH){
MotorBackward (); //Объект освобождаем –двигатели включаем на освобождение Motor=Backward // ждём пока не уберут БЛА, ждем по безопасности 5 секунд, чтобы уйти в режим ожидания БЛА while(getDist() > 100){
delay(5000);
}
flagCatch==false;
setColor(254,254,254);//белую подсветку включаем strDebug = strDebug + " Mode = StandBy";
}
if (strDebug !=""){
Serial.println (timeSecs + strDebug);
}
strDebug = "";
delay(10); // Delay a little bit to improve simulation performance
}
/***** конец кода программы *************/

Демонстрация работоспособности электроники и программных алгоритмов в виртуальной среде Tinkercad представлена в Таблице 4.1

Таблица 4. Фотографии/снимки экрана основных 4-х этапов работы эл. части Платформы
№п/п | Фото | Описание
1 | | Этап включения питания – инициализации: - подсветка светится белым - двигатель работает в обратном направлении –244RPM – захват раскрывается для перехода в режим ожидания

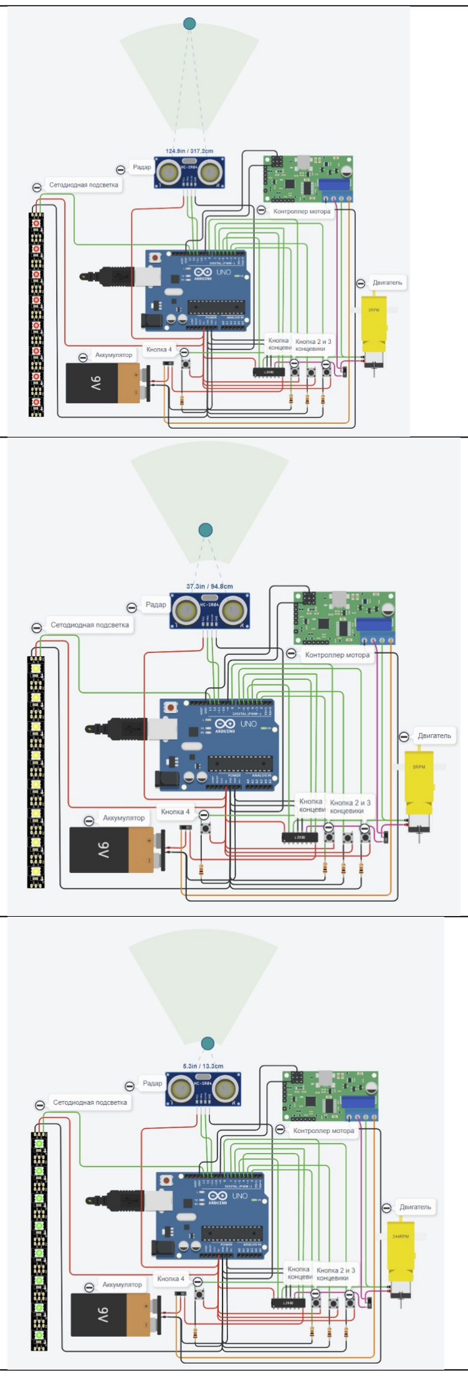
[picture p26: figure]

2 | Включился режим «этап захват цели» flagTarget=True: - радар показывает дальность до БЛА 317,2 см - подсветка светит красным
3 | включился режим предПосадка: - радар показывает дальность до БЛА 94,8 см - подсветка светит жёлтым
4 | Режим захвата БЛА: - радар показывает дальность до БЛА 13,3 см и неподвижность БЛА (сел) - подсветка светит зелёным - двигатель работает в прямом направлении 244RPM – толкатели сдвигаются для захвата и удержания БЛА

Заключение: в ходе выполнения Задания 4 разработано программное обеспечение для работы Платформы:
- написан код работы микроконтроллера с взаимодействием с основными элементами схемы, включая управление подсветкой посадочной платформы в зависимости от расстояния до приземляющегося квадрокоптера;
- разработан автоматический алгоритм работы Платформы, включающий программные сценарии.
5. Задание 5: Производство.
Определение необходимых материалов для изготовления посадочной платформы с учетом прочности и легкости.

Подробный перечень необходимых для изготовления Платформы материалов указан в Таблице 6.1. Стоимость материалов и работ.
Таблица 5.1. Основные используемые материалы и аргументация их выбора:
№ п/п | Наименование | Область применения | Аргументация выбора | Фото/эскиз
1 | Многослойная фанера 6 мм | используется для изготовления основной площадки -стола Платформы | • Выдерживает вес крупных БЛА, • при этом оставаясь легким материалом, • легка в обработке • изготовление через 3d печать неоптимально
2 | Элементы формируемые 3d печатью PLA пластиком | Держатели, муфты, крепёжные площадки, футляры для электронных компонентов | • точность и быстрота изготовления детале сложной формы • уменьшение разнообразия используемых мтериалов для унификации и организации производства
3 | Плата Arduino Uno | Управляющий контроллер | • недорогая • есть необходимая функциональность
4 | Электронные компоненты (дальномер) | Датчики и элементы управления | • совместимость с Arduino • обладает необходимой функциональностью
5 | Шаговый двигатель | Кинематика хватателей | обладает достаточным усилием для позиционирования и фиксации

Сборка Платформы
Таблица 5.2. Полноценная технологическая карта изготовления Платформы с последовательностью этапов изготовления.
№п/п, шаг опер-ции | Описание технологической операции | Эскиз | Материалы, Оборудование, инструменты и приспособления | Вр емя , ч
1 | Печать деталей на 3d принтере | | Пластик PLA 3d Принтер | 3
2 | Резка листов многослойной фанеры для изготовления корпуса | | Многослойная фанера и электролобзик (пильный инструмент) | 0,5
3 | В подготовленных листах | | Фреза по дереву и | 1

| многослойной фанеры делаются необходимы технологические вырезы и отверстия ИЛИ фрезеровка на ЧПУ станке | сверлильный станок (дрель) ИЛИ Лазерный/Фрезерный станок с ЧПУ
4 | Сборка каркаса платформы из деталей изготовленных на шаге 1 и шаге 3 | Ручной инструмент и электроинструмент | 1.5

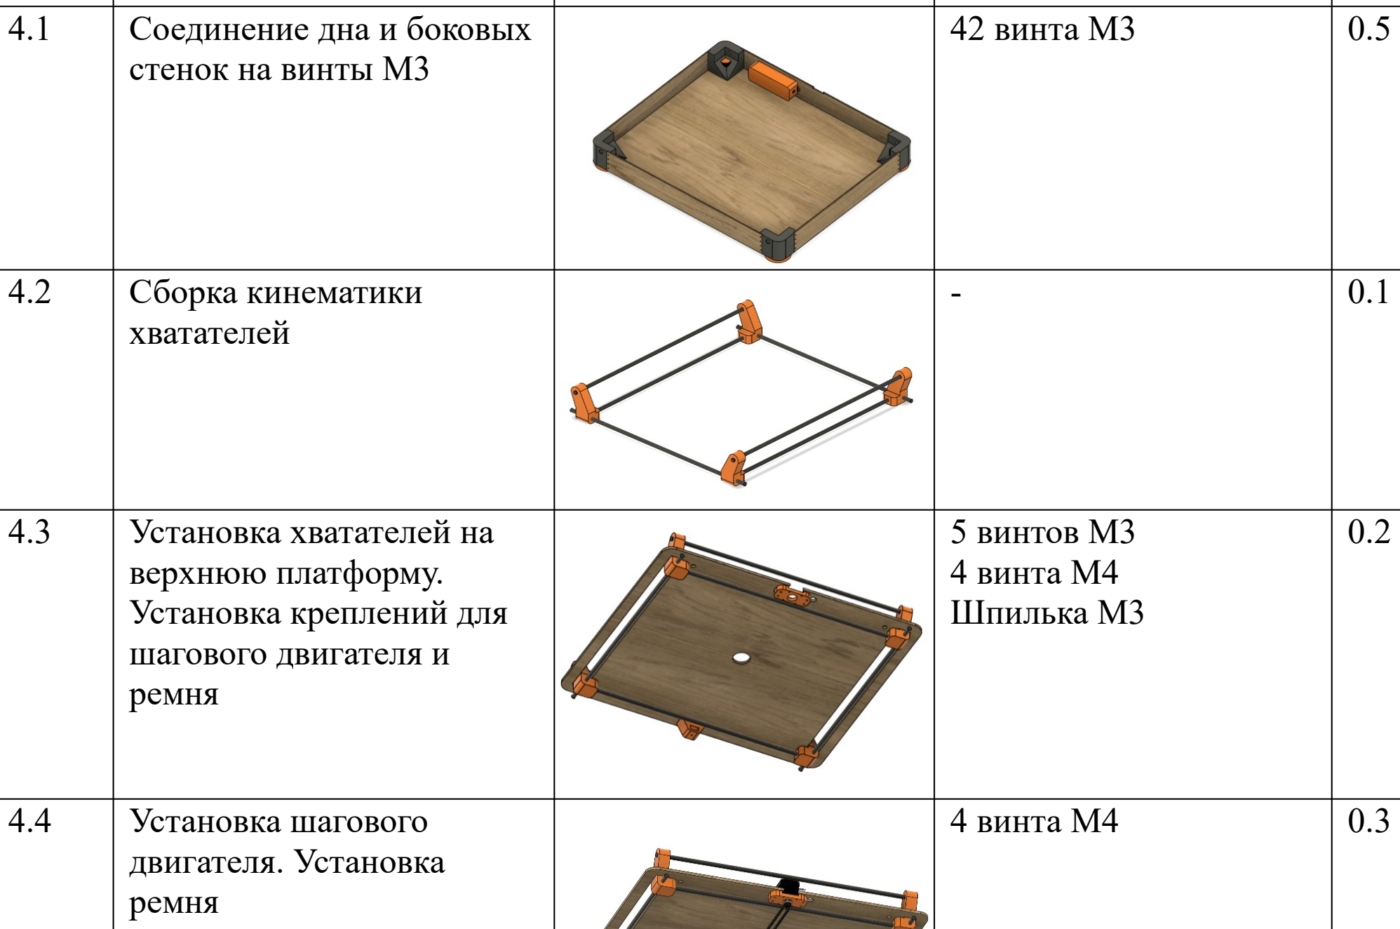
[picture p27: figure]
Сборка кинематики хватателей; Установка шагового двигателя. Установка ремня; 4 винта M4

4.1 | Соединение дна и боковых стенок на винты M3 | 42 винта М3 | 0.5
4.3 | Установка хватателей на верхнюю платформу. Установка креплений для шагового двигателя и ремня | 5 винтов М3 4 винта М4 Шпилька М3 | 0.2
4.5 | Установка LED ленты и сборка компонентов, полученных на шаге 4.4 и 4.1 Наклейка оранжевой виниловой пленки в форме буквы Н | 4 винта M4 | 0.4
5 | Пайка эл. элементов | Паяльная станция и необходимые компоненты (провода, припой и др.) | 1

6 | Установка электрических компонентов и их взаимное подключение | 2 винта М3 | 1
7 | Программирование Ардуино – заливка ПО | Компьютер, ПО | 0,1
8 | Тестовое включение, проверка базовой функциональности | | 0,1

Заключение: в ходе выполнения Задания 5 описан этап производства Платформы:
- описаны выбранные материалы
- аргументирован выбор материалов
- указано необходимое оборудование;
- создана полноценная технологическая карта изготовления Платформы с последовательностью этапов изготовления.
6. Задание 6. Бюджет.
Определение бюджета проекта.
Стоимость материалов и работ по изготовлению 1 шт Платформы
Таблица 6.1. Стоимость материалов и работ
№п/п | Наименование (ссылка на магазин) | Ед. | Кол-во | Цена за 1 ед., руб. | Стоим-ость, руб
| Материалы
1 | PLA пластик, чёрный (https://aliexpress.ru/item/1005003902556997.html?sku_id=12000027423382013) | кг | 1 | 1350 | 1350
2 | Многослойная фанера 6 мм (https://leroymerlin.ru/catalogue/fanera/laminirovannaya-6-mm/?00401=600.0&00405=600.0) 600*600*6 | шт | 1 | 1000 | 1000
3 | Arduino Uno R3 (https://arduinoshop.ru/arduino-uno-r3-328p) | шт | 1 | 600 | 600
4 | Комплект проводов, резисторы и разьёмы | | 1 | 1000 | 1000
5 | H-мост Драйвер управления шаговым двигателем motor control shield for Arduino (https://aliexpress.ru/item/32972605224.html?sku_id=12000023315235772) | шт | 1 | 900 | 900
6 | Шаговый двигатель Nema 17, 34 мм, 26 см (36,8 унций), а, 12 В, Nema17, шаговый двигатель 42BYGH, 4-проводной ЧПУ Reprap 3D-принтер | AliExpress (https://aliexpress.ru/item/32907886993.html?sku_id=65956580901&spm=.search_results.0.58b042d46Z9e8T) | шт | 1 | 900 | 900
7 | Ультразвуковой дальномер HC-SR04 (https://aliexpress.ru/item/1005003208661042.html?sku_id=12000024669213030) | шт | 1 | 57 | 57
8 | Макетная плата (https://market.yandex.ru/product--maketnaia-plata-mini-na-170-tochek/1401535476?sku=101392737405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) | шт | 1 | 147 | 147
9 | Кнопка тактовая 12х12 KLS7-TS1204 (https://www.yourduino.ru/product/knopka-kruglaya) | шт | 4 | 5 | 20
10 | Выключатель четырехконтактный KCD1-104 (https://www.yourduino.ru/product/vyklyuchatel-chetyrehkontaktnyy-kcd1-104) | шт | 1 | 35 | 35
11 | Светодиодная лента RGB , 5 v Модуль светодиодный Neopixel High Dtnsity 8 RGB (https://market.yandex.ru/product--modul-svetodiodnyi-neopixel-high-dtnsity-8-rgb-ws2812-5050/37243141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) | шт | 1 | 624 | 624

| WS2812 5050 (https://market.yandex.ru/product--modul-svetodiodnyi-neopixel-high-dtnsity-8-rgb-ws2812-5050/37243141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)
12 | Силовое реле - модуль реле: HJR-4102-L-5V Реле шилд 4х канальный (https://arduino54.ru/catalog/platy-moduli-shildy/rele/rele-shild-4h-kanalnyj-dlya-uno-i-mega2560/) | шт | 1 | 504 | 504
13й | Литиевые аккумуляторы, емкостью 2200 МА\Ч, с напряжением 12 В (https://aliexpress.ru/item/32824964556.html?sku_id=64887207216) | шт | 1 | 2300 | 2300
| Итого материалы | | | | 9497
| Работы
| Стоимость механика по сборке | 5 | ч | 500 | 2500
| Стоимость работ по монтажу электроники | 2 | ч | 1000 | 2000
| Итого работы | | | | 4500
| Итого | | | | 13997
Итого: 14 000 рублей
Заключение: в ходе выполнения Задания 6 рассчитана экономическая часть проекта, с составлением экономической сметы.
7. Заключение
Цель и задачи, поставленные в работе, выполнены. В результате данной работы исследованы варианты построения Платформы и управление её через Arduino. В процессе разработки Платформы были решены 6 заданий:
✓ Эскизное моделирование (чертёж);
✓ 3D-моделирование;
✓ Робототехническая часть;
✓ Программирование;
✓ Производство;
✓ Бюджет.
В конце работы опробован прототип Платформы.
Таким образом, можно сделать вывод, что разработанная Платформа выполняет заявленную цель проекта и решает поставленные задачи.
Основные технические характеристики разработанной Платформы:
Масса — 5 кг
Габариты:
Длина- 650 мм
Ширина- 550 мм
Высота- 140 мм

### 8. По итогам анализа разработанного прототипа Платформы были выявлены

следующие недостатки:
✓ Чувствительность аккумуляторов к холоду (резкое ухудшение характеристик аккумуляторов при низких температурах)
✓ Недостаточная защита от влаги. Корпус не герметичен, и при активных осадках в блок электроники может попасть вода и вывести оборудование из строя.

### 9. Эволюция и дальнейшие перспективы разработанной модели Платформы

Дальнейшее развитие платформы возможно в сторону повышения точности позиционирования и захвата, а также расширения области применений и ограничений по эксплуатации (влагозащита, температуростойкость, ударопрочность). Потребуется интеграция дополнительных датчиков.
Возможная модернизация:
✓ Датчики контакта приземления БЛА
✓ Лазерный дальномер
✓ Модуль WiFi
✓ Радиомаячок
✓ Радиомаячок

### 10. Список использованных источников

Список литературы
1. Сборник лучших работ 2022 года, МГТУ им. Баумана с XXV научно-образовательное соревнования «Шаг в будущее» (сборник лучших работ-2022.pdf)
2. Сборник лучших работ 2023, МГТУ им. Баумана, Центр довузовской подготовки МГТУ им. Баумана, Олимпиада школьников «Шаг в будущее» конференция «Шаг в будущее. космонавтика» XXVI научно-образовательное соревнование молодых исследователей «шаг в будущее» (best_2023.pdf)
3. Сборник, в который вошли лучшие статьи участников Научно- образовательного соревнования молодых исследователей «Шаг в будущее, Москва», проходившего 16-20 марта 2015 года в МГТУ им. Н.Э. Баумана. (bestworks2015_t2.pdf)
4. Сборник, в который вошли лучшие статьи участников Научно- образовательных соревнований молодых исследователей «Шаг в будущее, Москва» и «Шаг в будущее, Космонавтика», проходившего 12-16 марта 2018 года в МГТУ им. Н.Э. Баумана (Сборник лучших работы_2017-2018.pdf)
5. Сборник, в который вошли лучшие статьи участников Научно - образовательного соревнования молодых исследователей «Шаг в будущее», проходившего c 15 по 19 марта 2021 года в МГТУ им. Н.Э. Баумана (Сборник лучших работ-2021.pdf)
6. Проектная работа «Разработка счётчика посетителей» Е.Куреева, 2019 г.
Интернет – сайты:
7. Официальный сайт Ардуино URL: https://www.arduino.cc (дата обращения 08.03.2024)
8. Все об Ардуино URL: https://all-arduino.ru/ (дата обращения 08.03.2024)
9. Подключение ультразвукового датчика к Ардуино URL: http://роботехника18.рф/ультразвуковой-датчик-к-ардуино/ (http://xn--18-6kcdusowgbt1a4b.xn--p1ai/%D1%83%D0%BB%D1%8C%D1%82%D1%80%D0%B0%D0%B7%D0%B2%D1%83%D0%BA%D0%BE%D0%B2%D0%BE%D0%B9-%D0%B4%D0%B0%D1%82%D1%87%D0%B8%D0%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) (дата обращения 08.03.2024)
10. Подключение Arduino, установка драйвера URL:https://www.youtube.com/watch?v=E5a6iLrxAug (https://www.youtube.com/watch?v=E5a6iLrxAug) (дата обращения 08.03.2024)
11. Онлайн редактор макетов плат Fritzing URL: https://fritzing.org/ (дата обращения 08.03.2024)
12. Домики для дронов: какие посадочные платформы БПЛА бывают, что внутри, чем отличаются, кто делает и как выбрать нужную. Frontwise 9 окт 2020 URL: https://habr.com/ru/companies/innopolis/articles/521948/
13. https://www.tinkercad.com/

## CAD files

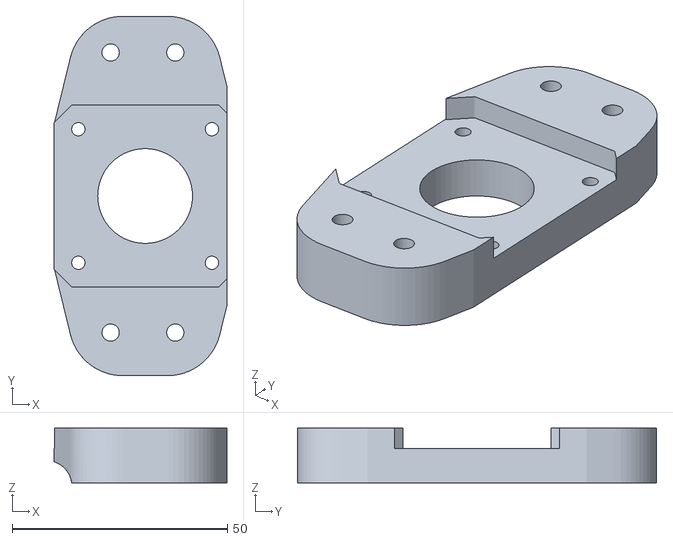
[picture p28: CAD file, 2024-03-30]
STL/ULP_ULP v21_MotorHolder.stl
40.1 x 83.4 x 12.7

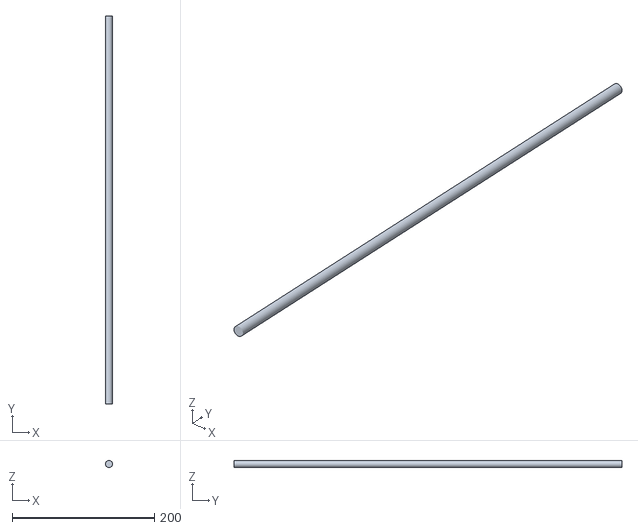
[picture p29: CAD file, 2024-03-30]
STL/ULP_ULP v21_Z_CarbonTubeRail_A.stl
10.0 x 545.0 x 9.97

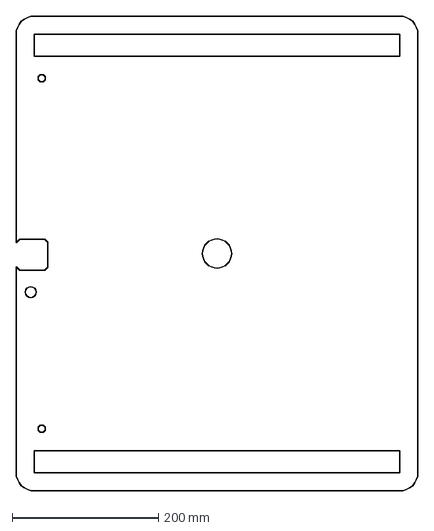
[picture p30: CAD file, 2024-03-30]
STL/1xLandingPlate-fanera_6mm.dxf
550.0 x 650.0 mm

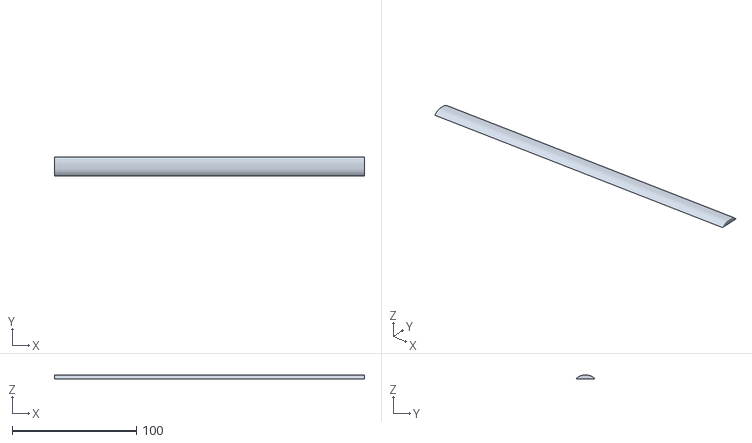
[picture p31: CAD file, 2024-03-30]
STL/ULP_ULP v21_LED_L.stl
250.0 x 15.0 x 3.00

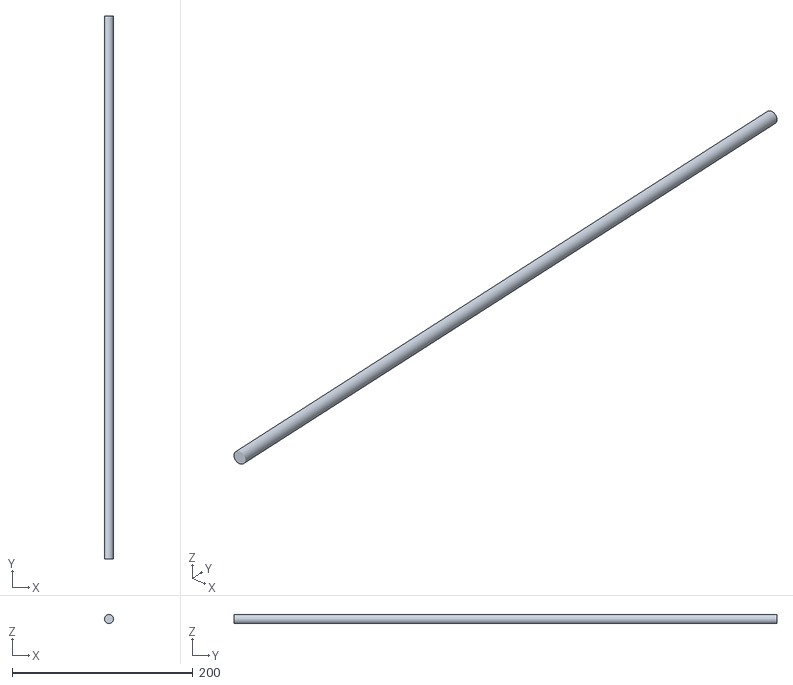
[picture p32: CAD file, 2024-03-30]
STL/ULP_ULP v21_CathingRod.stl
10.0 x 600.0 x 9.97

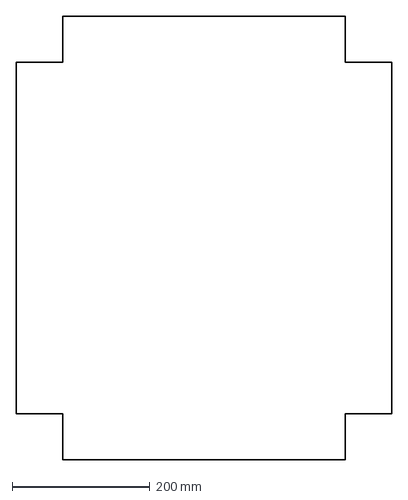
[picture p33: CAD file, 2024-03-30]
STL/1xBottomPlate-fanera_3mm.dxf
544.0 x 644.0 mm

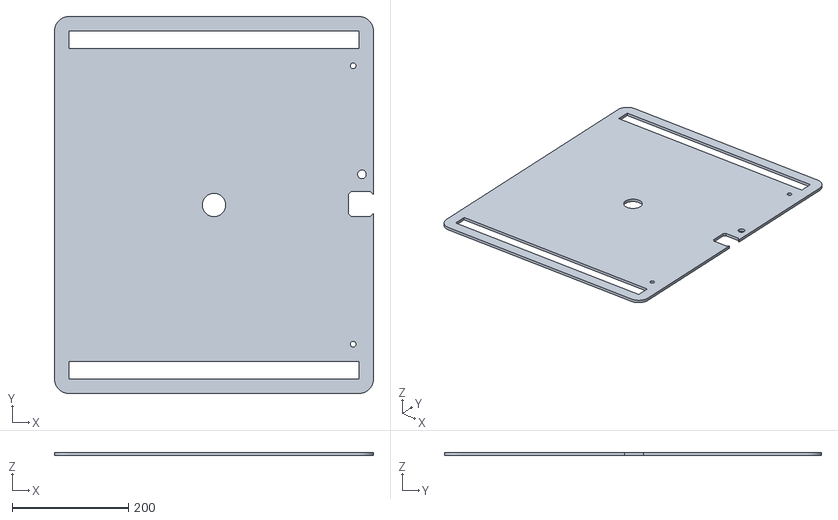
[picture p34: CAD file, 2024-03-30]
STL/ULP_ULP v21_LandingPlate.stl
550.0 x 650.0 x 6.00

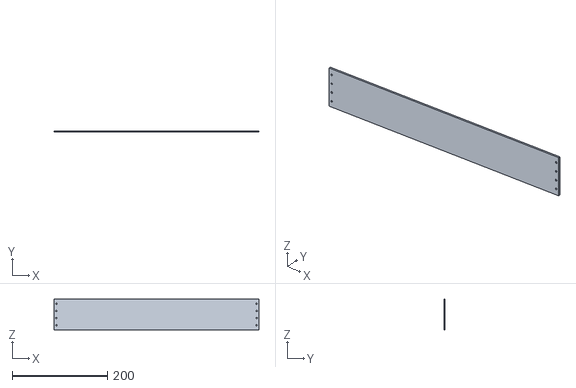
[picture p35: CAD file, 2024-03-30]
STL/ULP_ULP v21_Left_Wall.stl
430.0 x 3.00 x 65.0

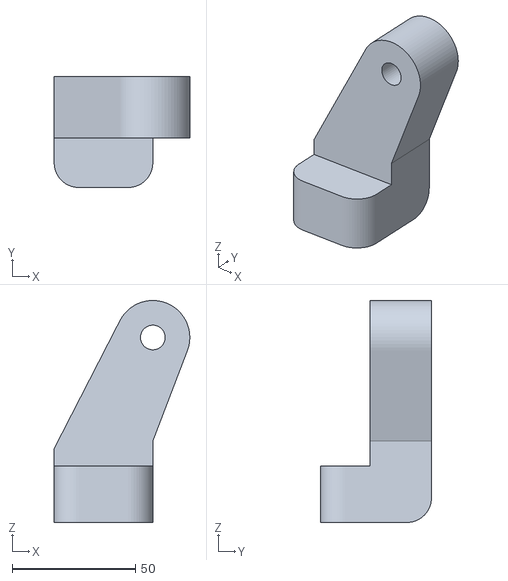
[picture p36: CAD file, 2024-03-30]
STL/ULP_ULP v21_Horn_RF.stl
55.0 x 45.0 x 90.0

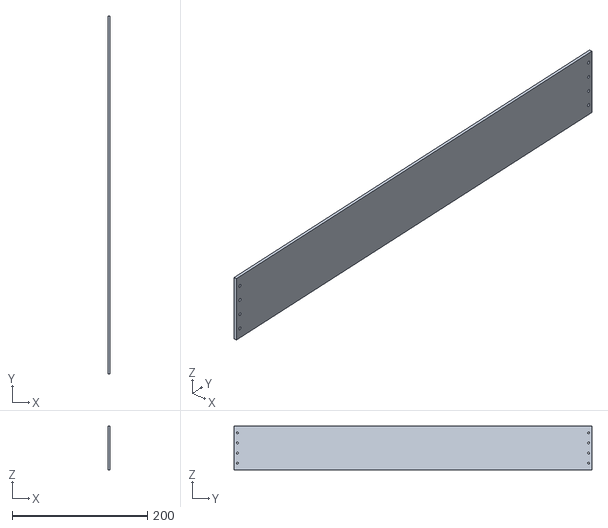
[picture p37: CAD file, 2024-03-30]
STL/ULP_ULP v21_Back_Wall.stl
3.00 x 530.0 x 65.0

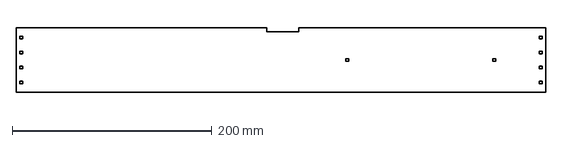
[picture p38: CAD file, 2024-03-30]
STL/2xFront_Wall-fanera_3mm.dxf
530.0 x 65.0 mm

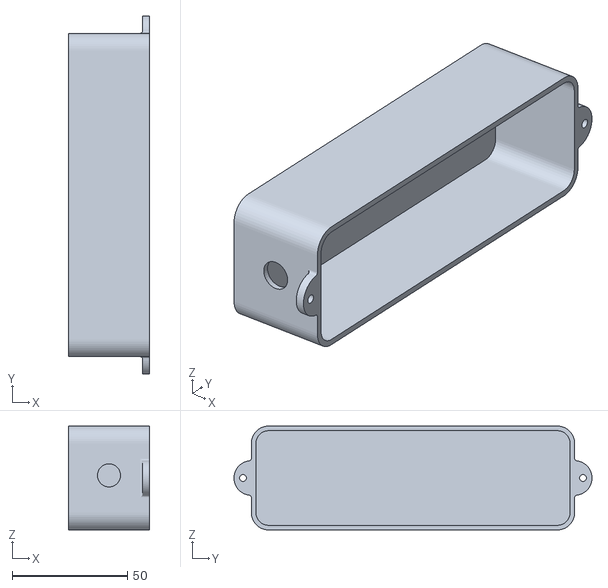
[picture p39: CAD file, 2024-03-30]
STL/ULP_ULP v21_ElecrtoBox.stl
35.0 x 155.0 x 45.0

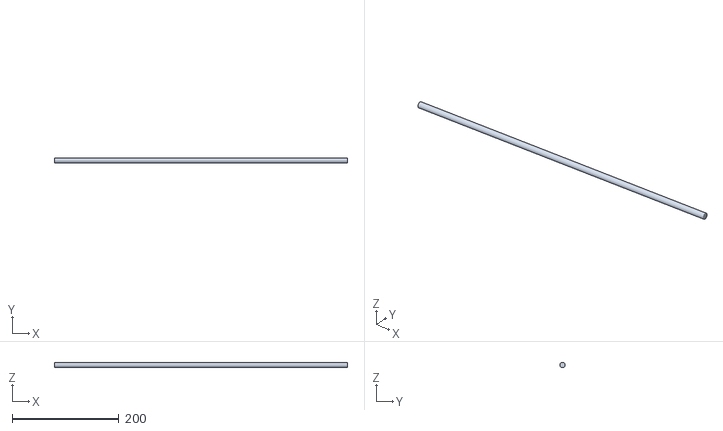
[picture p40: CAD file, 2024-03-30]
STL/ULP_ULP v21_X_CarbonTubeRail_B.stl
550.0 x 10.0 x 9.97

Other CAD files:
STL/ULP_ULP v21_CatchingRod_1.stl
STL/ULP_ULP v21_Right_Wall.stl
STL/ULP_ULP v21_Horn_LF.stl
STL/ULP_ULP v21_LED_R.stl
STL/ULP_ULP v21_Horn_RB.stl
STL/2xLeft_Wall-fanera_3mm.dxf
STL/ULP_ULP v21_Belt.stl
STL/ULP_ULP v21_BottomPlate.stl
STL/ULP_ULP v21_Front_Wall.stl
STL/ULP_ULP v21_Horn_LB.stl
STL/ULP_ULP v21_PulleyAxis.stl
STL/ULP_ULP v21_X_CarbonTubeRail_A.stl
STL/ULP_ULP v21_Z_CarbonTubeRail_B.stl

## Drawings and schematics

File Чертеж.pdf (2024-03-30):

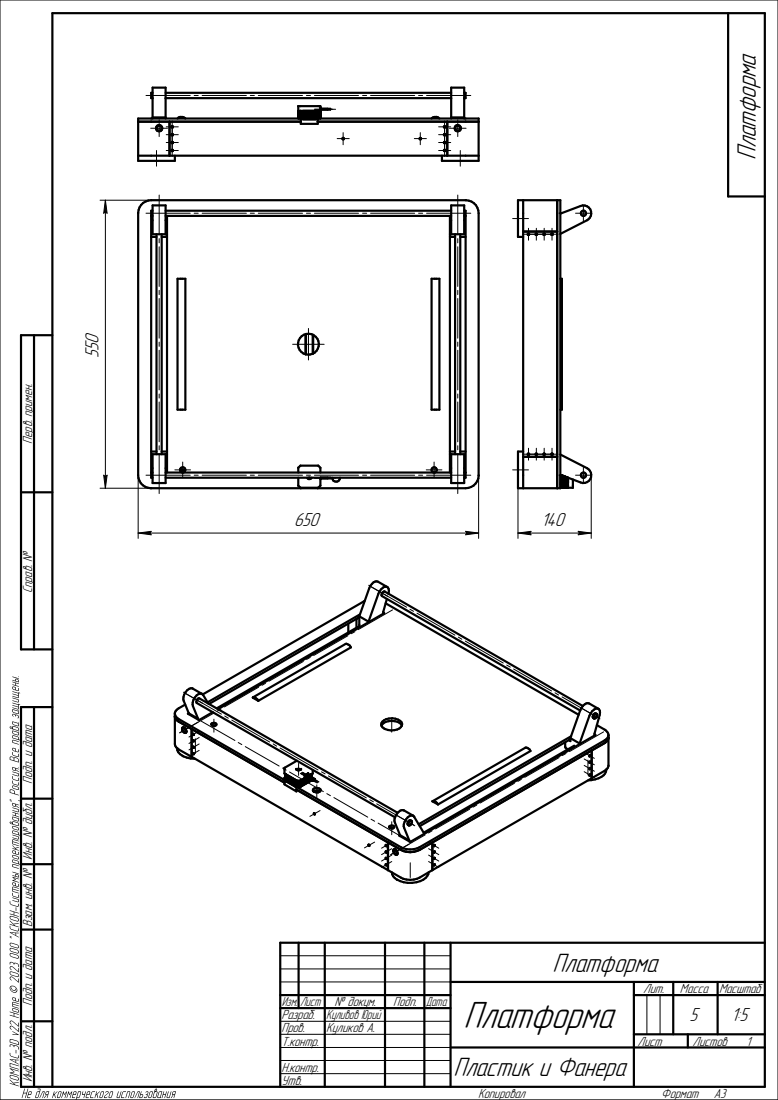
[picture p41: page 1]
650 ⁵⁵⁰; Пластик и Фанера Инв. № подл. Подп. и дата Взам. инв. № Инв. № дубл. Подп. и дата Справ. № Перв. примен.; Платформа Копировал; Формат A3

Платформа

Платформа | Лит. | Масса | Масштаб

Изм. Лист | № докум. | Подп. | Дата | | | | | 5 | 1:5 1
Разраб. | Куливов Юрий
Пров. | Куликов А.
Т.контр. | | | | Лист | Листов

Н.контр.
Утв.

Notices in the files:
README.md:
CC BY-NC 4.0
